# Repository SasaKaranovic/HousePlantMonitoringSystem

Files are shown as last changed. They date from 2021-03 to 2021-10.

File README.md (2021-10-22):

# DIY House Plants Watering System

## Part 1: Sensor board

DIY House Plants Watering System - Part 1: Sensor Board (https://youtu.be/ucjUwo17kw4)

Watch: [DIY House Plants Watering System // Part 1: Sensor Board](https://youtu.be/ucjUwo17kw4)

Blog page: https://sasakaranovic.com/blog/diy-house-plants-watering-system-part-1-sensor-board/

Build watering system for house plants. In part one of this video series, we will create a sensor that measures soil moisture, ambient temperature and light.

## Part 2: Central unit

DIY House Plants Watering System - Part 2: Central unit (https://youtu.be/RPgxssBxUtw)

Watch: [DIY House Plants Watering System // Part 2: Central unit](https://youtu.be/RPgxssBxUtw)

Blog page: https://sasakaranovic.com/projects/diy-house-plants-watering-system-part-2-central-unit/

Build watering system for house plants. In part two of this video series, we will create a central unit that takes sensor readings and also waters our plants on command.

## Part 3: Automation and Conclusion

DIY House Plants Watering System - Part 3: Automation and Conclusion (https://youtu.be/jLdTUMHOhRE)

Watch: [DIY House Plants Watering System // Part 2: Automation and Conclusion](https://youtu.be/jLdTUMHOhRE)

Blog page: https://sasakaranovic.com/projects/diy-house-plants-watering-system-part-3-automation/

Build watering system for house plants. In part two of this video series, we will create a central unit that takes sensor readings and also waters our plants on command.

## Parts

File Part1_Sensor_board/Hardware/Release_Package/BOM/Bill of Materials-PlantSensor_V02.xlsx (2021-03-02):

Designator | Description | Distributor | Distributor Part Number | Manufacturer | Manufacturer Part Number | Quantity
C1, C2, C5, C6, C7 | CAP CER 0.1UF 50V X7R 0603 | DigiKey | 1276-CL10B104KB8NNNLCT-ND | Samsung Electro-Mechanics | CL10B104KB8NNNL | 5
D1 | DIODE GEN PURP 100V 300MA SOD123 | DigiKey | 1N4148W-FDICT-ND | Diodes Incorporated | 1N4148W-7-F | 1
P1, P3 | CONN HEADER VERT 4POS 2.54MM | DigiKey | 732-5317-ND | Würth Elektronik | 61300411121 | 2
P2 | CONN HEADER VERT 6POS 2.54MM | DigiKey | 2057-PH2-06-UA-ND | Adam Tech | PH2-06-UA | 1
R1, R9, R10, R11 | RES SMD 4.7K OHM 1% 1/10W 0603 | DigiKey | 311-4.70KHRCT-ND | Yageo | RC0603FR-074K7L | 4
R2, R7 | RES SMD 10K OHM 1% 1/10W 0603 | DigiKey | 311-10KLDCT-ND | Yageo | AC0603FR-0710KL | 2
R4 | RES SMD 1K OHM 1% 1/10W 0603 | DigiKey | YAG2323CT-ND | Yageo | RT0603FRE071KL | 1
R5 | RES SMD 0 OHM JUMPER 1/10W 0603 | DigiKey | 311-0.0LECT-ND | Yageo | AC0603JR-070RL | 1
R6 | PHOTOCELL CDS 400OHM TO-18 | DigiKey | NSL-5152-ND | Advanced Photonix | NSL-5152 | 1
R8 | RES SMD 1M OHM 5% 1/10W 0603 | DigiKey | 311-1.0MGRCT-ND | Yageo | RC0603JR-071ML | 1
U1 | IC MCU 32BIT 16KB FLASH 32LQFP | DigiKey | 497-17480-ND | STMicroelectronics | STM32L011K4T6 | 1
U2 | SENSOR DIGITAL -55C-125C SOT23-5 | DigiKey | MCP9800A0T-M/OTCT-ND | Microchip Technology | MCP9800A0T-M/OT | 1

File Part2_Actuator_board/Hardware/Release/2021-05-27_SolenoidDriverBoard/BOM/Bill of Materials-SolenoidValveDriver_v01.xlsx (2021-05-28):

Designator | Description | Distributor | Distributor Part Number | Manufacturer | Manufacturer Part Number | Quantity
C1 | Capacitor | DigiKey | 1276-3051-1-ND | Samsung Electro-Mechanics | CL31A226MPHNNNE | 1
C2, C4, C5, C6, C7 | Capacitor, CAP CER 0.1UF 50V X7R 0603 | DigiKey | 1276-CL10B104KB8NNNLCT-ND | Samsung Electro-Mechanics | CL10B104KB8NNNL | 5
C3 | Capacitor | DigiKey | 1276-3091-1-ND | Samsung Electro-Mechanics | CL31B105KBHNFNE | 1
D1 | Typical RED GaAs LED | DigiKey | 732-4978-1-ND | Würth Elektronik | 150060RS75000 | 1
D2 | DIODE GEN PURP 100V 300MA SOD123 | DigiKey | 1N4148W-FDICT-ND | Diodes Incorporated | 1N4148W-7-F | 1
P1, P2 | Header, 5-Pin | DigiKey | 952-2246-ND | Harwin Inc. | M20-9960545 | 2
P4 | Header, 2-Pin | DigiKey | 952-2244-ND | Harwin Inc. | M20-9960245 | 1
Q1 | MOSFET N-CH 60V 0.38A | DigiKey | DMN62D0U-13DICT-ND | Diodes Incorporated | DMN62D0U-13 | 1
R1 | RES SMD 0 OHM JUMPER 1/10W 0603 | DigiKey | 311-0.0LECT-ND | Yageo | AC0603JR-070RL | 1
R4 | Resistor | DigiKey | 311-1.0KGRCT-ND | Yageo | RC0603JR-071KL | 1
R5 | RES SMD 1M OHM 5% 1/10W 0603 | DigiKey | 311-1.0MGRCT-ND | Yageo | RC0603JR-071ML | 1
U1 | IC MCU 8BIT 8KB FLASH 14SOIC | DigiKey | ATTINY814-SSNRCT-ND | Microchip Technology | ATTINY814-SSNR | 1

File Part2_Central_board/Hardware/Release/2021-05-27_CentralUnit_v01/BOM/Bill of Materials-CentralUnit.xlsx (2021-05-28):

Designator | Description | Distributor | Distributor Part Number | Manufacturer | Manufacturer Part Number | Quantity
C1, C2, C8, C9 | Polarized Capacitor (Axial) | DigiKey | 493-10673-1-ND | Nichicon | UKT1V101MED1TD | 4
C3, C5, C10, C11 | CAP CER 0.1UF 50V X7R 0603 | DigiKey | 1276-CL10B104KB8NNNLCT-ND | Samsung Electro-Mechanics | CL10B104KB8NNNL | 4
C4, C6, C7 | Capacitor | DigiKey | 493-13481-1-ND | Nichicon | UVZ1J220MDD1TD | 3
D1 | DIODE GEN PURP 100V 300MA SOD123 | DigiKey | 1N4148W-FDICT-ND | Diodes Incorporated | 1N4148W-7-F | 1
D2 |  | DigiKey | 478-7805-1-ND | AVX Corporation | SD1206S040S1R0 | 1
L1 | Shielded - Inductor 200mOhm Nonstandard | DigiKey | 240-2745-2-ND | Laird-Signal Integrity Products | TYS6045470M-10 | 1
P1 | TERM BLOCK HDR 5POS 90DEG 3.5MM | DigiKey | 732-2772-ND | Würth Elektronik | 691322110005 | 1
P2, P4 | 2 Position Terminal Block Header, Male Pins, Shrouded (4 Side) 0.138" (3.50mm) 90°, Right Angle - Through Hole | DigiKey | 732-2769-ND | Würth Elektronik | 691322110002 | 2
P3 | TERM BLOCK HDR 3POS 90DEG 3.5MM | DigiKey | 732-2770-ND | Würth Elektronik | 691322110003 | 1
P5, P6 | Header, 2-Pin | DigiKey | 952-2244-ND | Harwin Inc. | M20-9960245 | 2
Q1 | MOSFET N-CH 60V 0.38A | DigiKey | DMN62D0U-13DICT-ND | Diodes Incorporated | DMN62D0U-13 | 1
R1, R2, R3, R6, R7, R8, R9 | RES SMD 0 OHM JUMPER 1/10W 0603 | DigiKey | 311-0.0LECT-ND | Yageo | AC0603JR-070RL | 7
R5 | RES SMD 1M OHM 5% 1/10W 0603 | DigiKey | 311-1.0MGRCT-ND | Yageo | RC0603JR-071ML | 1
R10 | Resistor | DigiKey | 311-1.8KGRCT-ND | Yageo | RC0603JR-071K8L | 1
R11 | Resistor | DigiKey | 311-1.0KGRCT-ND | Yageo | RC0603JR-071KL | 1
U1 |  | TBD | TBD | Espressif | ESP32-Dev Module | 1
U2 | IC REDRIVER I2C 1CH 8TSSOP | DigiKey | 568-5926-1-ND | NXP USA Inc. | PCA9517ADP,118 | 1
U3 | Buck Switching Regulator IC Positive Fixed 3.3V 1 Output 3A TO-263-6, D²Pak (5 Leads + Tab), TO-263BA | DigiKey | LM2596S-3.3/NOPB-ND | Texas Instruments | LM2596S-3.3/NOPB | 1

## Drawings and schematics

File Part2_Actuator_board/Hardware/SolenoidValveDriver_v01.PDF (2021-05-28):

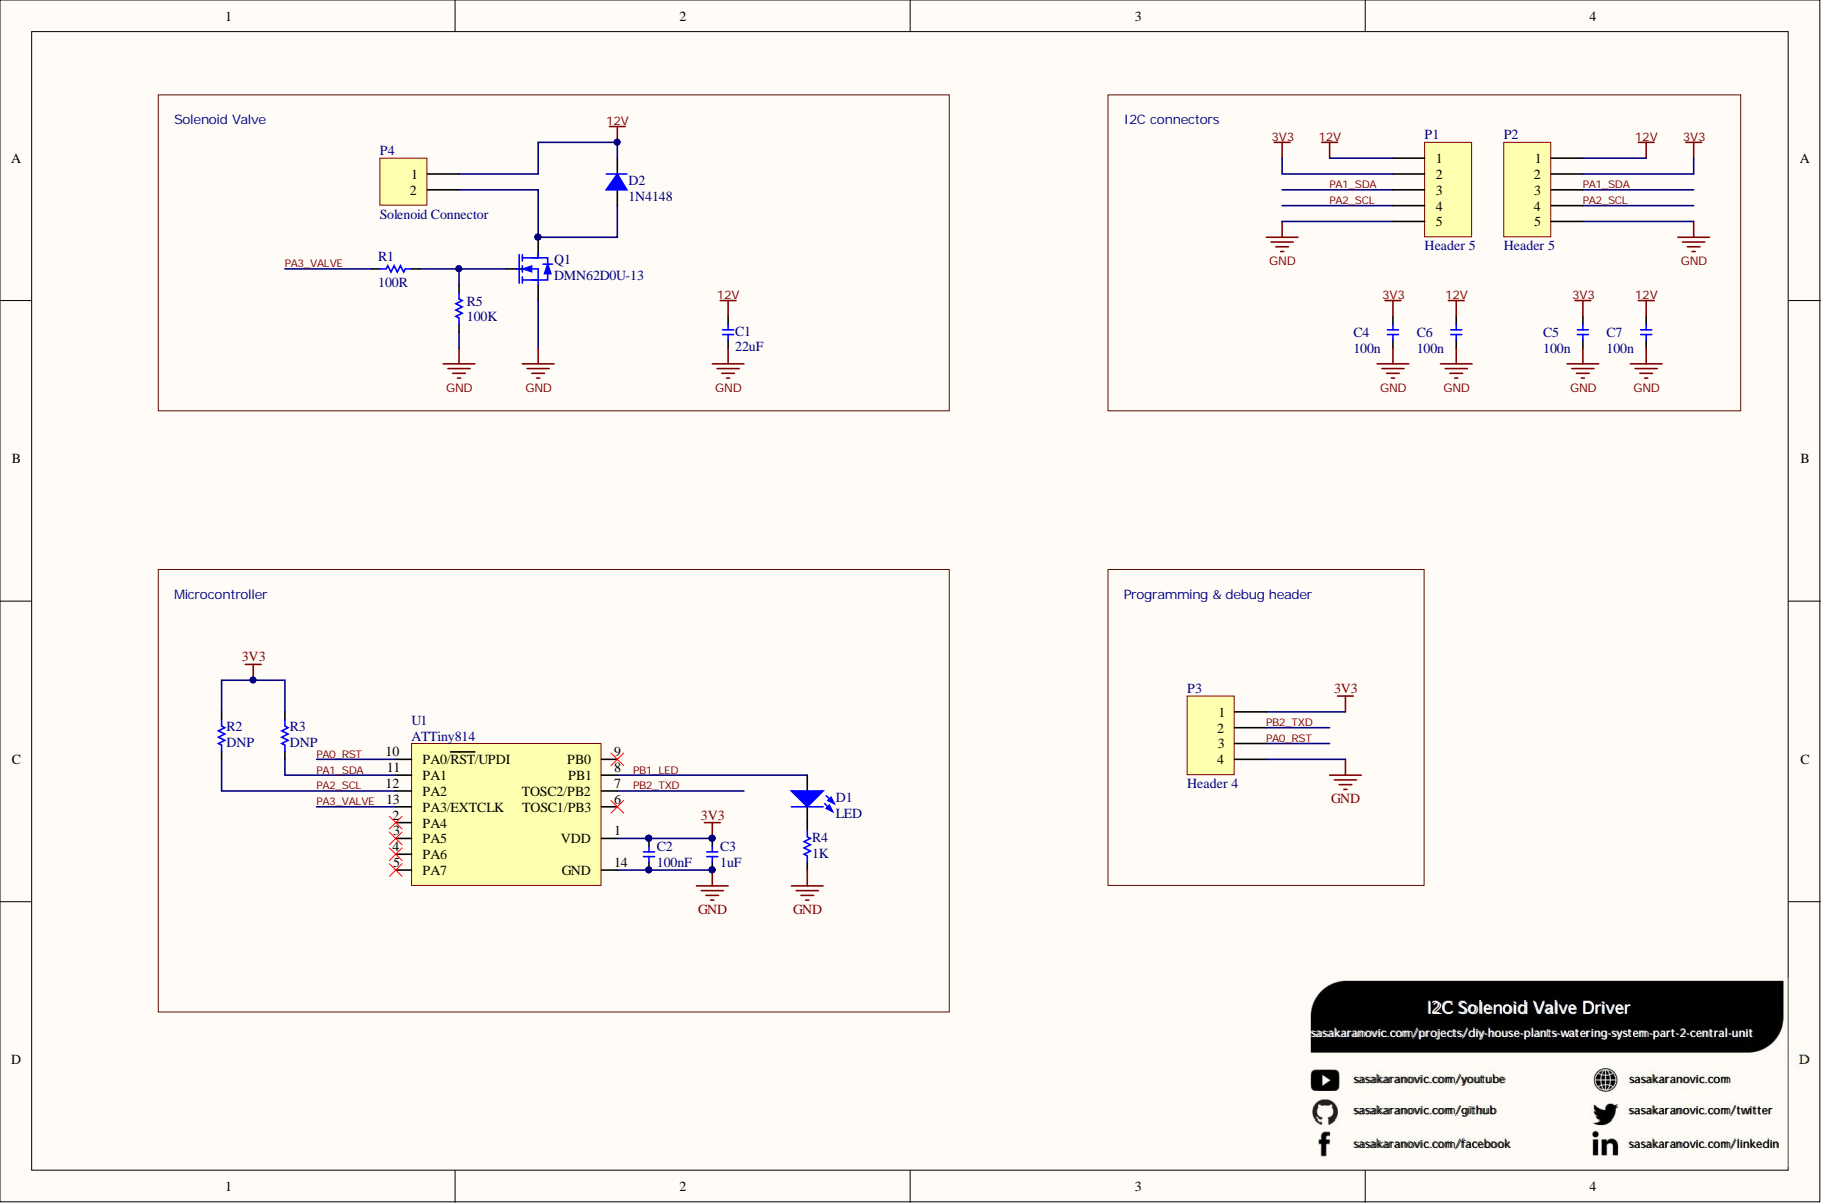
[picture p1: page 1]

sasakaranovic.com/projects/diy-house-plants-watering-system-part-2-central-unit

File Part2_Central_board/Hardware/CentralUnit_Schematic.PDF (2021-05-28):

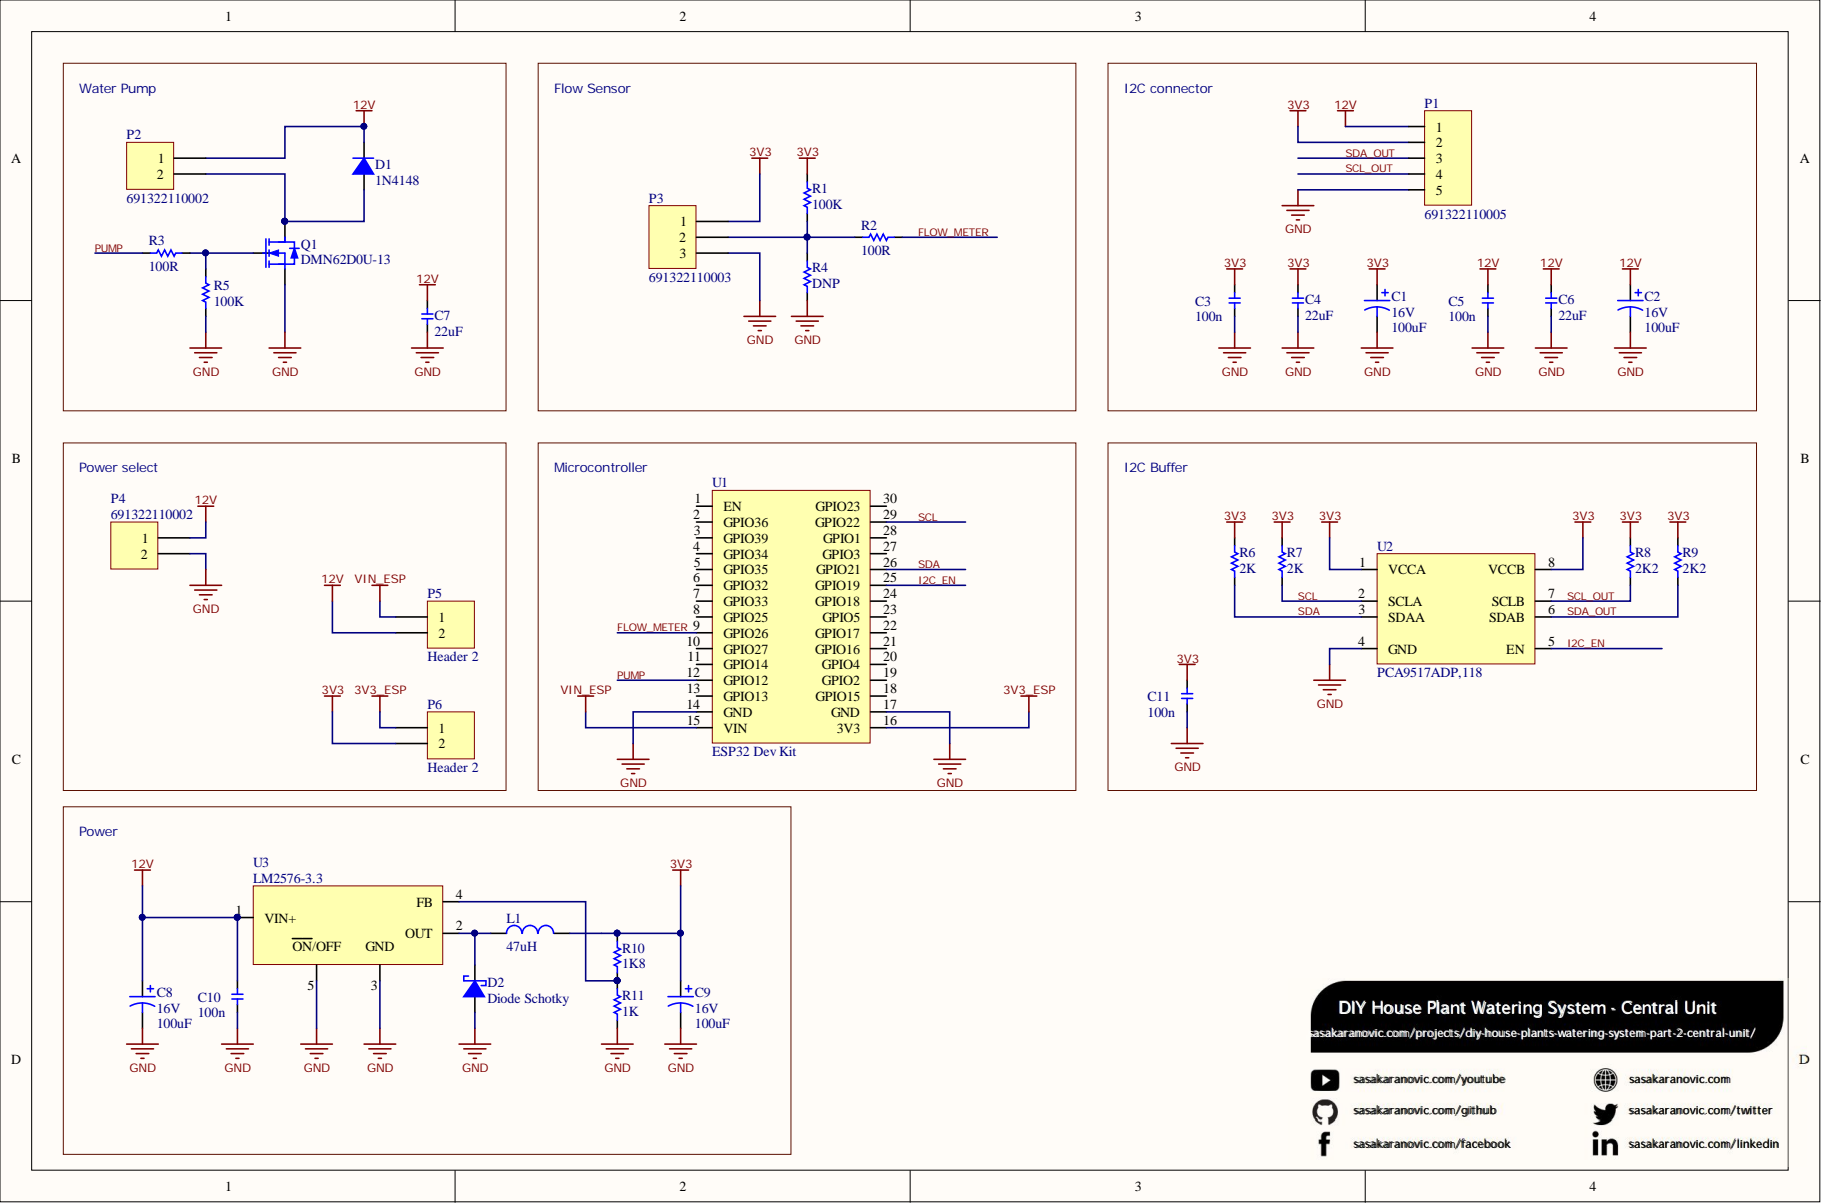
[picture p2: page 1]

DIY House Plant Watering System - Central Unit

sasakaranovic.com/projects/diy-house-plants-watering-system-part-2-central-unit/

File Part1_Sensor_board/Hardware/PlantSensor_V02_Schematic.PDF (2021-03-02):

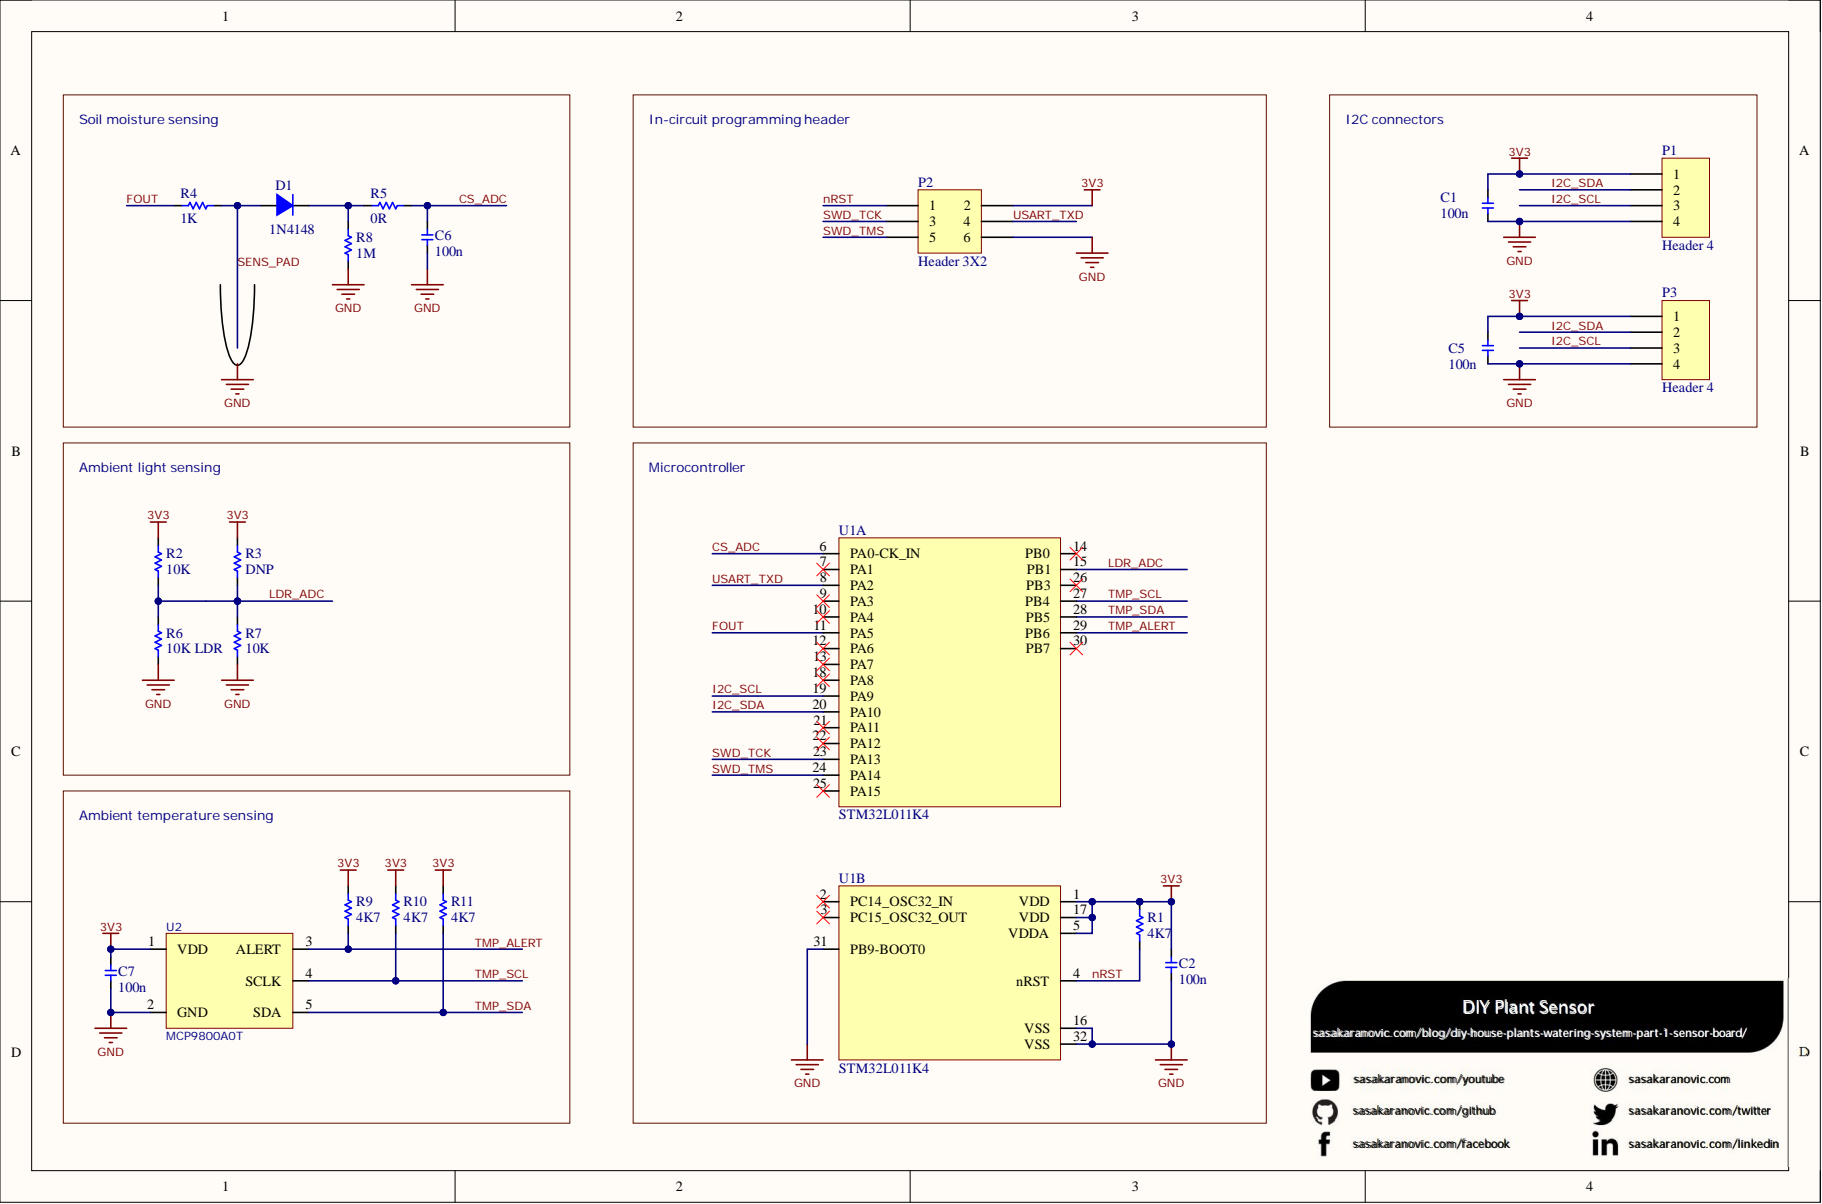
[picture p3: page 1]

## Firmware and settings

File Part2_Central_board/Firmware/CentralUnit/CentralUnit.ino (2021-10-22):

#include <EEPROM.h>
#include <SPIFFS.h>
#include <stdarg.h>
#include <stdio.h>
#include <esp_task_wdt.h>
#include <ESPmDNS.h>
#include "WiFi.h"
#include "ESPAsyncWebServer.h"
#include "CentralUnit_cfg.h"
#include "wifi_credentials.h"
#include "PlantSystem.h"
#include "Wire.h"
#include "time.h"
#include <WiFiUdp.h>
#include <ArduinoOTA.h>


#define WDT_TIMEOUT		20000
#define EEPROM_SIZE		4

const char* ntpServer = "pool.ntp.org";
const long  gmtOffset_sec = -18000;
const int   daylightOffset_sec = 3600;

AsyncWebServer server(80);
int WiFi_status = WL_IDLE_STATUS; 
volatile uint32_t nFlowSensorCount = 0;
volatile uint32_t nFlowSensorCount_last = 0;

char dbgBuff[4024] = {0};
uint32_t dbgBuffPos = 0;
float fImpulsePerML = WATERING_FLOW_EDGES_PER_mL;

void IRAM_ATTR ISR_flowSensor() {
    nFlowSensorCount++;
}

// Function prototypes
void ps_debug_log_reset_Reason(RESET_REASON reason);
void ps_debug_log_verbose_reset_reason(RESET_REASON reason);
int vprintf_into_spiffs(const char* szFormat, va_list args);
void printLocalTime();
void LOG_Timestamp(void);
void setupWebServer(void);
void flowInterruptEnabled(bool state);
void LED_Blink(uint8_t nTimes, uint16_t n_delayPeriod);
void PlantSystem_tick(void);
void PlantSystem_ScanBus(void);
void PlantSystem_debugShowDevicesOnBus(void);
void PlantSystem_getDeviceInfo(uint8_t devID);
bool PlantSystem_SetSolenoidState(uint32_t I2CAddress, bool energized);
void PlantSystem_UpdateSensors(void);
void I2C_SendBuffer(uint8_t address, uint8_t *pBuffer, uint8_t nLen);
bool I2C_ReadFrom(uint8_t address, uint8_t nLen, uint8_t *pData, uint8_t nPos, uint8_t nBytes);
bool PlantSystem_WaterPlant(uint8_t solenoidAddress, uint32_t n_volume_in_mL);
void PlantSystem_RequestPrimeSystem(void);
bool PlantSystem_PrimeSystemWithWater(void);
bool PlantSystem_WAPI_GetDevices(char *pBuff, uint32_t nMaxLen);
bool PlantSystem_WAPI_SensorData(char *pBuff, uint32_t nMaxLen);
bool PlantSystem_WAPI_SolenoidList(char *pBuff, uint32_t nMaxLen);



void setup()
{
	esp_task_wdt_init(30, true);

	pinMode(LED_PIN, OUTPUT);
	digitalWrite(LED_PIN, HIGH);

	pinMode(I2C_EN_PIN, OUTPUT);
	digitalWrite(I2C_EN_PIN, HIGH);
		
	pinMode(WATER_PUMP_EN_PIN, OUTPUT);
	digitalWrite(WATER_PUMP_EN_PIN, LOW);
		
	pinMode(FLOW_SENSOR_PIN, INPUT_PULLUP);
	
	Serial.begin(115200);

	// Setup Logging
	if (!SPIFFS.begin(true)) {
		Serial.println("An Error has occurred while mounting SPIFFS");
		while(1)
		{
			digitalWrite(LED_PIN, HIGH);
			delay(500);
			digitalWrite(LED_PIN, LOW);
			delay(500);
		}
	}
	else
	{
		Serial.println("SPIFFS mounted");

	}
	
	delay(500);
	esp_log_set_vprintf(&vprintf_into_spiffs);
	esp_log_level_set("*", ESP_LOG_DEBUG);
	esp_log_write(ESP_LOG_DEBUG, "SKWS", "-- SPIFFS Boot up\n");

	// Log reset reason
	Serial.println("Storing reason in log.txt");
	esp_log_write(ESP_LOG_DEBUG, "SKWS", "-- CPU0 ");
	ps_debug_log_verbose_reset_reason(rtc_get_reset_reason(0));
	esp_log_write(ESP_LOG_DEBUG, "SKWS", "-- CPU1 ");
	ps_debug_log_verbose_reset_reason(rtc_get_reset_reason(1));

	Wire.begin(I2C_SDA_PIN, I2C_SCL_PIN);

	// EEPROM begin
	EEPROM.begin(EEPROM_SIZE);

	// Debug EEPROM before read
	Serial.println("Before read: fImpulsePerML");
	Serial.println((float)(fImpulsePerML),4);
	
	// Read flow value from EEPROM
	fImpulsePerML = EEPROM.readFloat(0);
	
	// Debug EEPROM after read
	Serial.println("After read: fImpulsePerML");
	Serial.println((float)(fImpulsePerML),4);
	esp_log_write(ESP_LOG_DEBUG, "SKWS", "-- fImpulsePerML: %f\n", fImpulsePerML);


	// Configure WDT
	Serial.println("Configuring WDT...");
	esp_task_wdt_init(WDT_TIMEOUT, true); //enable panic so ESP32 restarts
	esp_task_wdt_add(NULL); //add current thread to WDT watch

	// Connect to WiFi
	esp_log_write(ESP_LOG_INFO, "SKWS", "-- Configuring WiFi.\n");
	WiFi.mode(WIFI_STA);
	WiFi.setHostname("sk_watering_system");
	esp_log_write(ESP_LOG_INFO, "SKWS", "-- Connecting to WiFi...\n");
	while ( WiFi_status != WL_CONNECTED) {
		Serial.print("Connecting to SSID: ");
		Serial.println(ssid);
		WiFi_status = WiFi.begin(ssid, password);

		esp_task_wdt_reset();

		digitalWrite(LED_PIN, HIGH);
		delay(500);
		digitalWrite(LED_PIN, LOW);
		delay(500);		
		digitalWrite(LED_PIN, HIGH);
		delay(500);
		digitalWrite(LED_PIN, LOW);
		delay(500);		
		digitalWrite(LED_PIN, HIGH);
		delay(500);
		digitalWrite(LED_PIN, LOW);
		delay(500);
	}
	esp_log_write(ESP_LOG_INFO, "SKWS", "-- Connected.\n");
	digitalWrite(LED_PIN, LOW);

	Serial.print("WiFi IP: ");
	Serial.println(WiFi.localIP());
	Serial.print("Hostname: ");
	Serial.println(WiFi.getHostname());

	char cIP_buff[50] = {0};
	String sIP = WiFi.localIP().toString();
	sIP.toCharArray(cIP_buff, 50);

	esp_log_write(ESP_LOG_DEBUG, "SKWS", "-- WiFi IP: %s\n", cIP_buff);
	esp_log_write(ESP_LOG_DEBUG, "SKWS", "-- WiFi hostname: %s\n",WiFi.getHostname());

	esp_log_write(ESP_LOG_DEBUG, "SKWS", "-- mDNS started\n");

	// Update time
	configTime(gmtOffset_sec, daylightOffset_sec, ntpServer);
	printLocalTime();
	LOG_Timestamp();

	// Config printout
	esp_log_write(ESP_LOG_DEBUG, "SKWS", "\n-- I2C_BUS_RESCAN_ENABLED=%d\n", I2C_BUS_RESCAN_ENABLED);
	esp_log_write(ESP_LOG_DEBUG, "SKWS", "-- PERIOD_RESCAN_BUS=%d\n", PERIOD_RESCAN_BUS);
	esp_log_write(ESP_LOG_DEBUG, "SKWS", "-- PERIOD_RELOAD_SENSORS=%d\n", PERIOD_RELOAD_SENSORS);
	esp_log_write(ESP_LOG_DEBUG, "SKWS", "-- FLOW_RATE_DEBUG_ENABLED=%d\n", FLOW_RATE_DEBUG_ENABLED);
	esp_log_write(ESP_LOG_DEBUG, "SKWS", "-- PERIOD_FLOW_RATE_DEBUG=%d\n\n", PERIOD_FLOW_RATE_DEBUG);

	digitalWrite(LED_PIN, LOW);

	setupWebServer();
	server.begin();
	esp_log_write(ESP_LOG_INFO, "SKWS", "-- Started web server.\n");

	MDNS.addService("http", "tcp", 80);

	ArduinoOTA.setHostname("WateringSystem");
	ArduinoOTA.setPassword("Tr6spEh1");

	ArduinoOTA
	.onStart([]() {
	  String type;
	  if (ArduinoOTA.getCommand() == U_FLASH)
	  {
	    type = "sketch";
	  }
	  else // U_SPIFFS
	  {
	    type = "filesystem";
	  	SPIFFS.end();
	  }

	  // NOTE: if updating SPIFFS this would be the place to unmount SPIFFS using SPIFFS.end()
	  Serial.println("Start updating " + type);
	})
	.onEnd([]() {
	  Serial.println("\nEnd");
	})
	.onProgress([](unsigned int progress, unsigned int total) {
	  Serial.printf("Progress: %u%%\r", (progress / (total / 100)));
	})
	.onError([](ota_error_t error) {
	  Serial.printf("Error[%u]: ", error);
	  if (error == OTA_AUTH_ERROR) Serial.println("Auth Failed");
	  else if (error == OTA_BEGIN_ERROR) Serial.println("Begin Failed");
	  else if (error == OTA_CONNECT_ERROR) Serial.println("Connect Failed");
	  else if (error == OTA_RECEIVE_ERROR) Serial.println("Receive Failed");
	  else if (error == OTA_END_ERROR) Serial.println("End Failed");
	});

	ArduinoOTA.begin();

	flowInterruptEnabled(true);
	esp_log_write(ESP_LOG_INFO, "SKWS", "-- Leaving setup.\n");
}


void flowInterruptEnabled(bool state)
{
	if(state)
	{
		attachInterrupt(FLOW_SENSOR_PIN, ISR_flowSensor, FALLING);
	}
	else
	{
		detachInterrupt(FLOW_SENSOR_PIN);
	}
}


void loop()
{
	ArduinoOTA.handle();
	PlantSystem_tick();
}



void setupWebServer(void)
{
	server.onNotFound([](AsyncWebServerRequest *request){
	  request->send(404);
	});

	// send a file when /index is requested
	server.on("/index.html", HTTP_ANY, [](AsyncWebServerRequest *request){
		request->send(200, "text/plain", "Plant System v0.1");
	});

	// send a file when / is requested
	server.on("/", HTTP_ANY, [](AsyncWebServerRequest *request){
		request->send(200, "text/plain", "Plant System v0.1");
	});


	// Read log.txt
	server.on("/log.txt", HTTP_GET, [](AsyncWebServerRequest *request){
		if(SPIFFS.exists("/log.txt")) 
		{
		  Serial.println("Log.txt request received");
	      request->send(SPIFFS, "/log.txt", "text/plain");
		} 
		else 
		{
	      request->send(200, "text/plain", "log.txt not found.");
	    }
	});

	// Delete /log.txt
	server.on("/delete_log", HTTP_GET, [](AsyncWebServerRequest *request){
		Serial.println("Delete Log.txt request received");
		if(SPIFFS.exists("/log.txt")) 
		{
			File writeLog = SPIFFS.open("/log.txt", FILE_WRITE);
			if(!writeLog) Serial.println("Couldn't open log.txt"); 
			delay(50);
			LOG_Timestamp();
			esp_log_write(ESP_LOG_DEBUG, "SKWS", "-- Log wiped.\n");
			writeLog.close();
			request->send(200, "text/plain", "log.txt reset");
		} 
		else 
		{
	      request->send(200, "text/plain", "log.txt not found.");
	    }
	});


	// Get sensors on the bus
	server.on("/sensorData", HTTP_GET, [] (AsyncWebServerRequest *request) {
		Serial.println("Sensor data");

		char buff[500] = {0};
		if(PlantSystem_WAPI_SensorData(buff, 500) == true)
		{
			request->send(200, "text/plain", buff);
			return;
		}
		else
		{
			Serial.println("PlantSystem_WAPI_SensorData() error");
			request->send(200, "text/plain", "PlantSystem_WAPI_SensorData() FAIL");
			return;
		}
	});

	// Get solenoids on the bus
	server.on("/solenoidData", HTTP_GET, [] (AsyncWebServerRequest *request) {
		Serial.println("Solenoid data");

		char buff[500] = {0};
		if(PlantSystem_WAPI_SolenoidList(buff, 500) == true)
		{
			request->send(200, "text/plain", buff);
			return;
		}
		else
		{
			Serial.println("PlantSystem_WAPI_SolenoidList() error");
			request->send(200, "text/plain", "PlantSystem_WAPI_SolenoidList() FAIL");
			return;
		}
	});


	// Get devices on the bus
	server.on("/deviceData", HTTP_GET, [] (AsyncWebServerRequest *request) {
		Serial.println("Device data");

		char buff[500] = {0};
		if(PlantSystem_WAPI_GetDevices(buff, 500) == true)
		{
			request->send(200, "text/plain", buff);
			return;
		}
		else
		{
			Serial.println("PlantSystem_WAPI_GetDevices() error");
			request->send(200, "text/plain", "PlantSystem_WAPI_GetDevices() FAIL");
			return;
		}
	});

	// Get number of flow sensor ticks for last watering action
	server.on("/flowSensor", HTTP_GET, [] (AsyncWebServerRequest *request) {
		Serial.println("Flow sensor data");

		char buff[100] = {0};
		int len;
		len = snprintf(buff, 100, "{flowSensor:%d}", nFlowSensorCount_last);

		if(len>0)
		{
			request->send(200, "text/plain", buff);
			return;
		}
		else
		{
			Serial.println("PlantSystem_WAPI_GetDevices() error");
			request->send(200, "text/plain", "nFlowSensorCount FAIL");
			return;
		}
	});


	// Set solenoid state
	server.on("/setSolenoid", HTTP_GET, [] (AsyncWebServerRequest *request) {
		Serial.println("Set solenoid to state");

		if ( request->hasParam("address") && request->hasParam("state") )
		{
			String xAddress;
			String xState;

			uint32_t nAddress 	= 0;
			uint32_t nState 	= 0;

			xAddress = request->getParam("address")->value();
			nAddress = xAddress.toInt();

			xState = request->getParam("state")->value();
			nState = xState.toInt();

			if(PlantSystem_SetSolenoidState(nAddress, nState) == true)
			{
				request->send(200, "text/plain", "OK");
				return;
			}
			else
			{
				Serial.println("PlantSystem_SetSolenoidState() error");
				request->send(200, "text/plain", "PlantSystem_SetSolenoidState() FAIL");
				return;
			}
		}
		else
		{
			request->send(200, "text/plain", "MISSING ARGUMENTS");
			return;
		}
	});

	// Water plant connected to solenoid with X ml of water
	server.on("/waterPlant", HTTP_GET, [] (AsyncWebServerRequest *request) {
		Serial.println("Water plant request");

		if ( request->hasParam("address") && request->hasParam("volume") )
		{
			String xAddress;
			String xVolume;

			uint32_t nAddress 	= 0;
			uint32_t nVolume 	= 0;

			xAddress = request->getParam("address")->value();
			nAddress = xAddress.toInt();

			xVolume = request->getParam("volume")->value();
			nVolume = xVolume.toInt();

			if(PlantSystem_WaterPlant(nAddress, nVolume) == true)
			{
				char buff[200] = {0};
				int len = 0;

				len = snprintf(buff, 200, "{ \"result\": OK, \"Address\":%d, \"Volume\":%d }", 
															nAddress, nVolume);
				request->send(200, "text/plain", buff);
				UNUSED(len);
				return;
			}
			else
			{
				Serial.println("PlantSystem_WaterPlant() error");
				request->send(200, "text/plain", "PlantSystem_WaterPlant() FAIL");
				return;
			}
		}
		else
		{
			request->send(200, "text/plain", "MISSING ARGUMENTS");
			return;
		}
	});


	// Prime the system with water
	server.on("/PrimeSystemWithWater", HTTP_GET, [] (AsyncWebServerRequest *request) {
		Serial.println("PlantSystem_RequestPrimeSystem()");

		PlantSystem_RequestPrimeSystem();
		request->send(200, "text/plain", "OK");
		return;
	});

	// Calibrate flow sensor or read current value
	server.on("/calibrateFlowSensor", HTTP_GET, [] (AsyncWebServerRequest *request) {
		Serial.println("Calibrate edges per mL");

		char buff[200] = {0};

		if ( request->hasParam("edges") )
		{
			String xEdges;
			float fEdges = 0;

			xEdges = request->getParam("edges")->value();
			fEdges = xEdges.toFloat();

			// Update value
			fImpulsePerML = fEdges;
			EEPROM.writeFloat(0, fEdges);//EEPROM.put(address, param);
			EEPROM.commit();

			Serial.print("Changing fImpulsePerML to ");
			Serial.println((float)(fImpulsePerML),4);

			snprintf(buff, 200, "New value set to %f", fEdges);
			request->send(200, "text/plain", buff);
			return;
		}
		else
		{
			snprintf(buff, 200, "Current value is %f\r\nLast impulse count was: %d", fImpulsePerML, nFlowSensorCount_last);
			request->send(200, "text/plain", buff);
			return;
		}
	});
}


void LED_Blink(uint8_t nTimes, uint16_t n_delayPeriod)
{
	while(nTimes--)
	{
		digitalWrite(LED_PIN, HIGH);
		delay(n_delayPeriod);

		digitalWrite(LED_PIN, LOW);
		delay(n_delayPeriod);
	}
}

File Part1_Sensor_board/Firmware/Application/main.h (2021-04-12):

#ifndef __MAIN_H
#define __MAIN_H

#include "stm32l0xx_hal.h"
#include <stdbool.h>

void Error_Handler(void);

#define VCP_TX_Pin 						GPIO_PIN_2
#define VCP_TX_GPIO_Port 				GPIOA
#define TMS_Pin 						GPIO_PIN_13
#define TMS_GPIO_Port 					GPIOA
#define TCK_Pin 						GPIO_PIN_14
#define TCK_GPIO_Port 					GPIOA
#define VCP_RX_Pin 						GPIO_PIN_15
#define VCP_RX_GPIO_Port 				GPIOA
#define LD3_Pin 						GPIO_PIN_3
#define LD3_GPIO_Port 					GPIOB
#define TEMP_ALERT_Pin 					GPIO_PIN_6
#define TEMP_ALERT_GPIO_Port 			GPIOB


/* Definition for I2Cx */
#define I2Cx                            I2C1
#define RCC_PERIPHCLK_I2Cx              RCC_PERIPHCLK_I2C1
#define RCC_I2CxCLKSOURCE_SYSCLK        RCC_I2C1CLKSOURCE_SYSCLK
#define I2Cx_CLK_ENABLE()               __HAL_RCC_I2C1_CLK_ENABLE()
#define I2Cx_SDA_GPIO_CLK_ENABLE()      __HAL_RCC_GPIOB_CLK_ENABLE()
#define I2Cx_SCL_GPIO_CLK_ENABLE()      __HAL_RCC_GPIOB_CLK_ENABLE() 

#define I2Cx_FORCE_RESET()              __HAL_RCC_I2C1_FORCE_RESET()
#define I2Cx_RELEASE_RESET()            __HAL_RCC_I2C1_RELEASE_RESET()

/* Definition for I2Cx Pins */
#define I2Cx_SCL_PIN                    GPIO_PIN_9
#define I2Cx_SCL_GPIO_PORT              GPIOA
#define I2Cx_SDA_PIN                    GPIO_PIN_10
#define I2Cx_SDA_GPIO_PORT              GPIOA
#define I2Cx_SCL_SDA_AF                 GPIO_AF1_I2C1

/* Definition for I2Cx's NVIC */
#define I2Cx_IRQn                       I2C1_IRQn
#define I2Cx_IRQHandler                 I2C1_IRQHandler


#endif

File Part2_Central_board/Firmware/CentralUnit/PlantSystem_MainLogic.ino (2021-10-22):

#include "CentralUnit_cfg.h"


// Every device that we saw on the bus
I2C_Device_TypeDef gDevicesOnBus[I2C_MAX_DEVICES_ON_BUS] = { {.i2cAddress=0, .deviceType=0} };
uint8_t gDevicesOnBusCount = 0;

// All sensors that are registered on the bus
I2C_Sensor_TypeDef gSensorsOnBus[I2C_MAX_SENSORS_ON_BUS] = { {.i2cAddress=0, .temperature=0.0, .soilMoisture=0, .ambienLight=0} };
uint8_t gnSensorsOnBusCnt = 0;

// All solenoids that are on the bus
I2C_Solenoid_TypeDef gSolenoidsOnBus[I2C_MAX_SOLENOIDS_ON_BUS] = { {.i2cAddress=0, .lastState=0} };
uint8_t gnSolenoidsOnBusCnt = 0;

// PlantSystem_tick global variables
uint32_t nPeriod_Rescanbus=0;
uint32_t nPeriod_ReloadSensors=0;
uint32_t nPeriod_FlowRate=0;

// Watering global variables
bool bPrimeSystem_requestPending=false;
bool bWatering_requestPending=false;
bool bWatering_inProgress=false;
bool bCloseValvesOnPowerUp=false;
bool bI2CBusScanned=false;
uint32_t nWatering_volume=0;
uint8_t nWatering_i2cAddress=0;
uint32_t nTimeout = 0;


void PlantSystem_tick(void)
{
	bool bWateringError = false;
	esp_task_wdt_reset();

	// -- Initial I2C scan
	if(bI2CBusScanned == false)
	{
		esp_task_wdt_reset();
		PlantSystem_ScanBus();
		PlantSystem_debugShowDevicesOnBus();
		bI2CBusScanned = true;
	}

	// -- I2C periodic rescan
	#if (I2C_BUS_RESCAN_ENABLED != 0)
	if(nPeriod_Rescanbus  <= millis())
	{
		esp_task_wdt_reset();
		PlantSystem_ScanBus();
		PlantSystem_debugShowDevicesOnBus();
		nPeriod_Rescanbus = millis() + PERIOD_RESCAN_BUS;
	}
	#endif

	// -- Reload sensor data
	if(nPeriod_ReloadSensors <= millis())
	{
		PlantSystem_UpdateSensors();
		nPeriod_ReloadSensors = millis() + PERIOD_RELOAD_SENSORS;
	}


	// -- Close all solenoids on boot
	if(bCloseValvesOnPowerUp == false)
	{
		// Turn OFF all solenoids
		delay(500);
		esp_task_wdt_reset();
		Serial.println("De-energizing ALL solenoids");
		for(uint8_t i=0; i<gnSolenoidsOnBusCnt; i++)
		{
			if (PlantSystem_SetSolenoidState(gSolenoidsOnBus[i].i2cAddress, false) == true)
			{
				Serial.print("Closed solenoid 0x");
				Serial.println(gSolenoidsOnBus[i].i2cAddress, HEX);
			}
			else
			{
				Serial.print("Failed to close solenoid 0x");
				Serial.println(gSolenoidsOnBus[i].i2cAddress, HEX);
			}
			delay(500);
		}
		bCloseValvesOnPowerUp = true;
	}

	#if (FLOW_RATE_DEBUG_ENABLED != 0)
	// -- Flow sensor debug
	if(nPeriod_FlowRate <= millis())
	{
		Serial.print("nFlowSensorCount: ");
		Serial.println(nFlowSensorCount, DEC);
		nPeriod_FlowRate = millis() + PERIOD_FLOW_RATE_DEBUG;
	}
	#endif

	// -- Process watering request
	if(bWatering_requestPending || bWatering_inProgress)
	{
		//	Watering logic
		//  Pump creates high pressure inside watering system. Because of this
		//	at the beginning of watering process we will first, open valve, then turn on pump.
		//	When we are done, we will first turn off pump and then solenoid.
		//
		//	In previous version, water pump was too weak so we turned on the pump first to keep the pressure on
		//	and prevent water from "backing up" (i.e letting air in from plant side).
		//	With peristaltic pump we can open the solenoids first and still keep air out of the system.
		//

		Serial.println("bWatering_requestPending | bWatering_inProgress");
		// Transition to in progress
		bWatering_inProgress = true;
		bWatering_requestPending = false;
		nFlowSensorCount = 0;

		// - Open solenoid
		Serial.println("Energizing solenoid");
		if (PlantSystem_SetSolenoidState(nWatering_i2cAddress, true) != true)
		{
			bWatering_requestPending = false;
			bWatering_inProgress = false;
			digitalWrite(WATER_PUMP_EN_PIN, LOW);
			Serial.println("Turning pump OFF");
			Serial.println("Failed to open solenoid. Aborting...");
			esp_log_write(ESP_LOG_ERROR, "SKWS", "-- Failed to open solenoid 0x%02X. Aborting...\n", nWatering_i2cAddress);
			LED_Blink(4, 250);
			return;
		}


		delay(2000);
		// - Reset flow counter
		nFlowSensorCount = 0;
		flowInterruptEnabled(true);
		
		// - Turn ON pump
		bWateringError = true;
		Serial.println("Turning pump ON");
		digitalWrite(WATER_PUMP_EN_PIN, HIGH);

		esp_task_wdt_reset();
		nTimeout = millis() + 20000;	// 20sec time-out for watering
		
		// Calculate water flow
		uint32_t nWaterFlow_millis_timestamp = millis();
		float flowMilliLitres = 0.0;
		uint32_t totalMilliLitres = 0;

		// Wait until target mL or timeout is reached
		while(millis() < nTimeout)
		{
			// Calculate mL every second
			if( millis() >= nWaterFlow_millis_timestamp)
			{
				// Disable interrupts
				flowInterruptEnabled(false);

				// Update mL
				if(fImpulsePerML <= 0)
				{
					Serial.println("Invalid fImpulsePerML value! Please calibrate flow sensor!");
					esp_log_write(ESP_LOG_ERROR, "SKWS", "-- Invalid fImpulsePerML value (fImpulsePerML=%f)! Please calibrate flow sensor!\n", fImpulsePerML);
					fImpulsePerML = 100;
				}
				flowMilliLitres = nFlowSensorCount/fImpulsePerML;
				totalMilliLitres += flowMilliLitres;

				// Check if target has been reached
				if(totalMilliLitres >= nWatering_volume)
				{
					bWateringError = false;
					break;
				}
				
				// Update for next iteration
				nWaterFlow_millis_timestamp = millis() + 1000;
				nFlowSensorCount = 0;
				esp_task_wdt_reset();
				flowInterruptEnabled(true);
			}
		}
		esp_task_wdt_reset();

		// - Turn OFF pump
		digitalWrite(WATER_PUMP_EN_PIN, LOW);
		Serial.println("Turning pump OFF");
		delay(200);

		// - Close solenoid
		Serial.println("De-Energizing solenoid");
		PlantSystem_SetSolenoidState(nWatering_i2cAddress, false);


		// Store last flow data and prepare for new request



		nFlowSensorCount_last = nFlowSensorCount;
		nFlowSensorCount = 0;
		nWatering_volume = 0;

		// Reset request
		bWatering_inProgress = false;
		bWatering_requestPending = false;
		if(bWateringError)
		{
			LED_Blink(4, 250);
		}
		else
		{
			LED_Blink(2, 500);
		}
	}


	// -- Process prime system with water request
	if(bPrimeSystem_requestPending)
	{
		esp_task_wdt_reset();
		PlantSystem_PrimeSystemWithWater();
		bPrimeSystem_requestPending = false;
	}
}
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

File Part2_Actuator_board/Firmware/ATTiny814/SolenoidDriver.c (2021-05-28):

#include "SolenoidDriver.h"
#include "PlantSystem.h"
#include "debug.h"
#include "mcc_generated_files/include/twi0_slave.h"

// -- Global definitions

// -- Extern variables
extern uint8_t TWI_TxBuff[TWI_BUFFER_SIZE];
extern uint8_t TWI_TxLen;
extern uint8_t TWI_TxPos;

extern uint8_t TWI_RxBuff[TWI_BUFFER_SIZE];    // Device RX from host
extern uint8_t TWI_RxPos;

// Solenoid turn-off timer
extern volatile uint32_t milliseconds;
extern volatile uint32_t solenoidTurnOff_target;
extern volatile bool bWDTRunning;

// CMD (1byte) + DATATYPE (1byte) + DATALEN (2bytes) 
void SolenoidDriver_ProcessRequest(uint8_t *pRxBuff, uint8_t nLen)
{
#if 0
  debugStr("pRxBuff:\r\n");
  for(uint8_t i=0; i<nLen; i++)
  {
      debugHex(pRxBuff[i]);
  }
#endif

    // First byte is always command
    switch(pRxBuff[0])
    {
        // -- Get device information
        case CMD_GET_DEVICE_INFO:
        {
            debugStr("\r\nInfo\r\n");
            TWI_TxBuff[0]  = 0xFF;                  // First byte is 0xFF to allow compatibility with STM and disable clock strech
            TWI_TxBuff[1]  = CMD_GET_DEVICE_INFO;   // Second byte is response to command
            TWI_TxBuff[2]  = DATATYPE_SINGLE_VALUE;
            TWI_TxBuff[3]  = 0;
            TWI_TxBuff[4]  = 2;
            TWI_TxBuff[5]  = DEVICETYPE_SOLENOID_V1;
            TWI_TxBuff[6]  = 1;
            TWI_TxLen = 7;
        }
        break;

        // -- SET solenoid state
        case CMD_SET_SOLENOID_STATE:
        {
            debugStr("\r\nSET State: ");

            // Data Type `DATATYPE_SINGLE_VALUE` and exactly 0 + 1 = 1 bytes
            if(pRxBuff[1] == DATATYPE_SINGLE_VALUE && pRxBuff[2] == 0 && pRxBuff[3] == 1)
            {
                debugHex(pRxBuff[1]);

                if(pRxBuff[4] == 0)
                {
                    debugStr("Turn OFF\r\n");
                    Solenoid_SET_Off();
                    Solenoid_ActLED_Off();
                }
                else
                {
                    debugStr("Turn ON\r\n");
                    Solenoid_SET_On();
                    Solenoid_ActLED_On();
                    SolenoidWDT_Activate();
                }
            }
            else
            {
                debugStr("Bad Data\r\n");
            }

        }
        break;

        // -- GET solenoid state
        case CMD_GET_SOLENOID_STATE:
        {
            debugStr("\r\nGET state\r\n");  

            TWI_TxBuff[0]  = 0xFF;                     // First byte is 0xFF to allow compatibility with STM and disable clock strech
            TWI_TxBuff[1]  = CMD_GET_SOLENOID_STATE;   // Second byte is response to command
            TWI_TxBuff[2]  = DATATYPE_SINGLE_VALUE;
            TWI_TxBuff[3]  = 0;
            TWI_TxBuff[4]  = 1;
            TWI_TxBuff[5]  = Solenoid_GetState();
            TWI_TxLen = 6;
        }
        break;

        // Catch-all
        default:
            debugStr("Uknown CMD received\r\n");
        break;
    }
}


void SolenoidWDT_Activate(void)
{
    solenoidTurnOff_target = milliseconds + SOLENOID_ON_TIMEOUT;
    bWDTRunning = true;
}

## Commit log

2021-02-26 Initial commit.
    [PlantSensor_V02.PrjPcb, PlantSensor_V02_PCB.PcbDoc, PlantSensor_V02_Schematic.SchDoc]
2021-02-26 Adding schematic .pdf output.
2021-03-02 Adding release/manufacturing package.
    [Bill of Materials-PlantSensor_V02.xlsx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]
2021-04-12 Modifying I2C logic. Restructuring code for readability. Adding new PlantSystem devices.
2021-04-14 Updating I2C comms.
2021-05-28 Part 2 Development
    Adding solenoid close timeout. Closing all solenoids on power-up.
    Central unit and Solenoid valve release
    [Bill of Materials-CentralUnit.xlsx, Bill of Materials-SolenoidValveDriver_v01.xlsx, CentralUnit.PrjPcb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]
2021-07-10 Adding http support to calibrate flow sensor
2021-10-22 Fixing missing files: Adding adjustable flow and logging.
    [CentralUnit.ino, CentralUnit_cfg.h, PlantSystem_Logging.ino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]
